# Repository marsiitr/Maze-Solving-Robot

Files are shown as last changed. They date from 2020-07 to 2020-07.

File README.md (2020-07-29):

# Maze-Solving-Robot
Srishti 2020

## Abstract

The Maze Solving Bot is a wireless bot. It is capable of solving any 2-D maze with the help of live video feed parsed by a python script. The speciality of this bot is that it can adapt itself to any maze and not one-kind in particular. Having a Four-wheel Omni drive, It aims to reach the ending point in the shortest time. If there are more than two ways out, then it works to solve the shortest path.

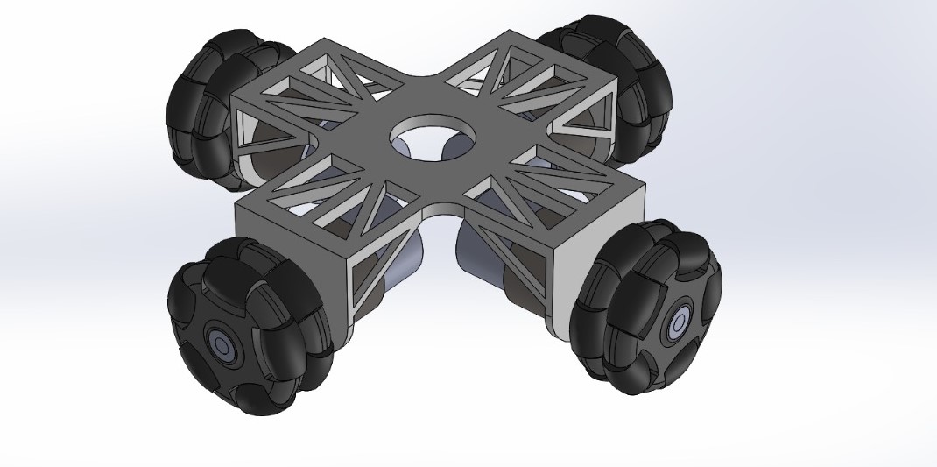
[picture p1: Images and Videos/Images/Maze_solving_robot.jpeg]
Final Product


## Motivation

<p align="justify">Maze solving bot is a simple and straightforward case where we can learn and experiment about path planning. The standard method of maze solving takes much time due to its trial and error methods. With the help of shortest path detection and robot live coordinates mapping, we look forward to improvising the olden methods.<br><br>A maze in the real-world can represent roads and traffic. All of us want to know the best way to go to work, school etc.  In the journey, we experience all sorts of obstructions like traffic, diversions, intersections and dead-ends. This project gives us an insight into how to solve this problem. It helps us find the best and the shortest path to avoid these barricades as much as possible.</p>

## Components

* 2x Motor Driver L2899
* 4x DC () rpm Motors
* Nodemcu Esp8266
* 1x 12V DC Power Adapter
* 3D printed Chassis
* 4x Omni Wheels

## Workflow

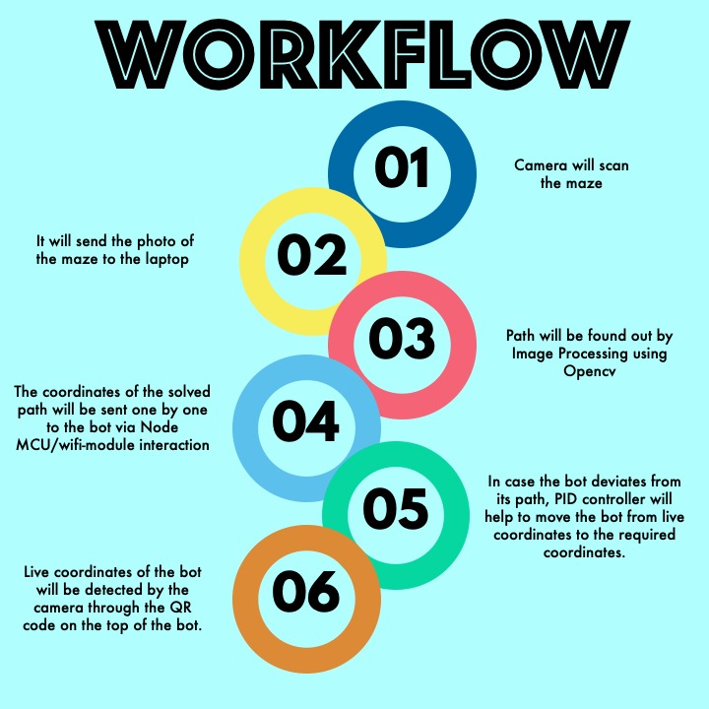
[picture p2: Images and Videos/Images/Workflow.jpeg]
Worflow Diagram


## Mechanical Aspect of the Design

### Chassis

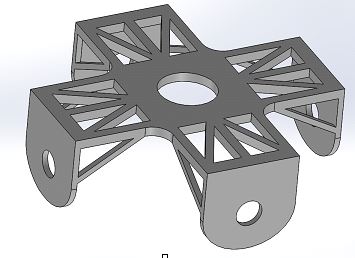
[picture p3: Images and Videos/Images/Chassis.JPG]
Chasis


<p align="justify">The main body of the robot is 3D printed using PLA(Polylactic Acid). It has the shape of a ‘plus’ sign. The dimensions of the chassis are about 14.5cm x 14.5cm x 5 cm. There are lightening holes present wherever possible to keep the weight of the chassis less</p>

### Drive type

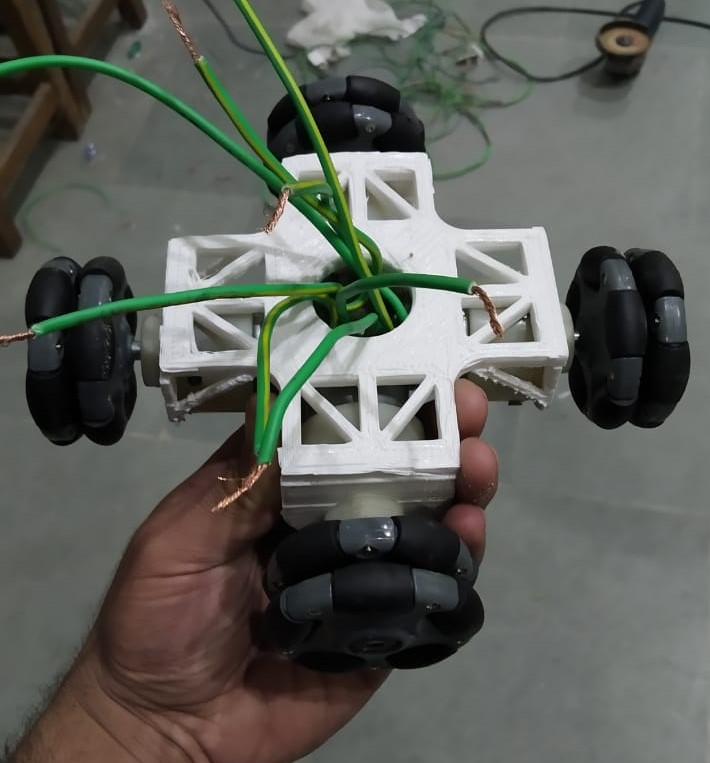
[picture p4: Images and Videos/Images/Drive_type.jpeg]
Drive _type


<p align="justify">The maze solving bot uses a 4 wheeled Omni type of drive. 2 sets of Omni wheels are perpendicular to the other set. The reason for this design is that the maze only consists of perpendicular junctions. Hence the working of the robot is highly simplified if we use 4 WD Omni.<br><br> 4 WD Omni in general has some limitations. It only takes 3 points to define a plane. Hence in most practical cases, the 4th wheel lies out of the plane. But in this project, we could dodge this limitation by 3D printing the chassis thus making it highly accurate.</p>

## Electronics Aspect of the Design

### Actuator

The robot uses four 12 volt- 100 rpm motors. These motors are relatively light, weighing a few hundred grams and overall have a small and compact size. Having a small body size is imperative for the robot to transverse through the narrow lanes of the maze..

### Microcontroller

* One of the biggest benefits of the NodeMCU is that it allows communication over a wifi-network, hence there is no need to keep it plugged into the device on which the source code is, the instructions can be easily sent over a wifi network.
* This allows the execution of the PID control equation to a significantly higher degree of precision.
* Completing both the tasks of receiving coordinates and controlling motors is done by Nodemcu. Coordinates are detected by scanning QR code.

### PID Control

* The PID control allows monitoring the progression of errors in the movements of the robot and making minute changes in the operation of the actuators to ensure a greater degree of precision in the robot’s movements.
* In our case, the robot had to move parallel to the co-ordinate axis only on a flat surface with minimal skidding of the wheels. This simplified our job many-fold, since now we focus only on the “proportional errors”, without considering the derivative of the integral terms.

## Cost Structure

| *Components* |*Cost(INR.)*|
|---|---|
| 2x Motor Driver L2899 | 250 |
| 2x DC () rpm Motors | 700 |
| Nodemcu Esp8266 | 350 |
| 12v Battery | 1000 |
| 3D printed Chassis | 800 |
| 4x Omni Wheels | 2200 |
| *Total* | *5300*  |

## Applications

* Reduce manual labour in waiting in hotels and in deliveries.
* Can be used in parking lots to direct the cars to the closest empty space.
* Future of driving is self-driving cars or fully automated cars 

## Limitations

* The Camera that we are using for image processing is attached to our laptop with wires, so that might become a bit hectic to handle.
* There has to be a minimum height above which Camera should be mounted, so for our maze solving bot show we need a spacious room, and we have to deal with a bunch of extra wires.

## Future Improvements

* Sensors can be added to the bot to avoid further immediate obstacles.

## Team Members

1. Akshat Gupta
2. [Sarthak Surolia](https://github.com/sarthak1420)
3. Sidhhart Gehlot
4. [Shanmathi Selvaraj](https://github.com/shan-mathi)
5. [Sneha Jain](https://github.com/snehajain02)
6. [Susmit Walve](https://github.com/susmitwalve)
7. [Suhani Jain](https://github.com/jainsuhani317)
8. [Yash Asati](https://github.com/yashasati53)

## Mentors

1. [Sanjeev Krishnan R.](https://github.com/SanjeevKrishnan)
2. Shubham Malviya

## References

<https://www.learnopencv.com/opencv-qr-code-scanner-c-and-python/>

<https://youtu.be/0u78hx-66Xk>

<https://github.com/marsiitr/DIC_Terrace_Farming>

<https://www.instructables.com/id/Controlling-Arduino-with-python-based-web-API-No-p/>

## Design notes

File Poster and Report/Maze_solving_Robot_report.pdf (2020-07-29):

# Maze solving Robot

## Srishti 2020 Project Report

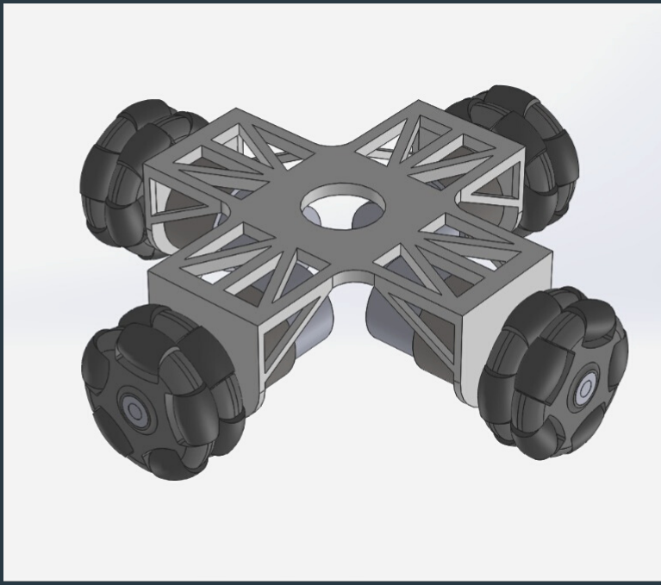
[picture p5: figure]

# INDEX

Team Members | 01
Abstract | 02
Motivation | 02
Workflow | 03
Mechanical aspects | 04
Electronic aspects | 05
Cost Structure | 08
Applications | 09
Limitations | 09
Further Improvements | 09
References | 10

# Team Members:

# Akshat Gupta Sarthak Surolia Shanmathi Selvaraj Siddharth Gehlot Sneha Jain Suhani Jain Susmit Walve Yash Asati

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
# Mentors:

Sanjeev Krishnan R.

# Shubham Malviya

1.
2.

1

# Abstract

The Maze Solving Bot is a wireless bot. It is capable of solving any 2-D maze with the help of live video feed parsed by a python script. The speciality of this bot is that it can adapt itself to any maze and not one-kind in particular. Having a Four-wheel Omni drive, It aims to reach the ending point in the shortest time. If there are more than two ways out, then it works to solve the shortest path.

# Motivation

Maze solving bot is a simple and straightforward case where we can learn and experiment about path planning. The standard method of maze solving takes much time due to its trial and error methods. With the help of shortest path detection and robot live coordinates mapping, we looked forward to improvise the olden methods.

A maze in the real-world can represent roads and traffic. All of us want to know the best way to go to work, school etc. In the journey, we experience all sorts of obstructions like traffic, diversions, intersections and dead-ends. This project gives us an insight into how to solve this problem. It helps us find the best and the shortest path to avoid these barricades as much as possible

2

# Workflow:

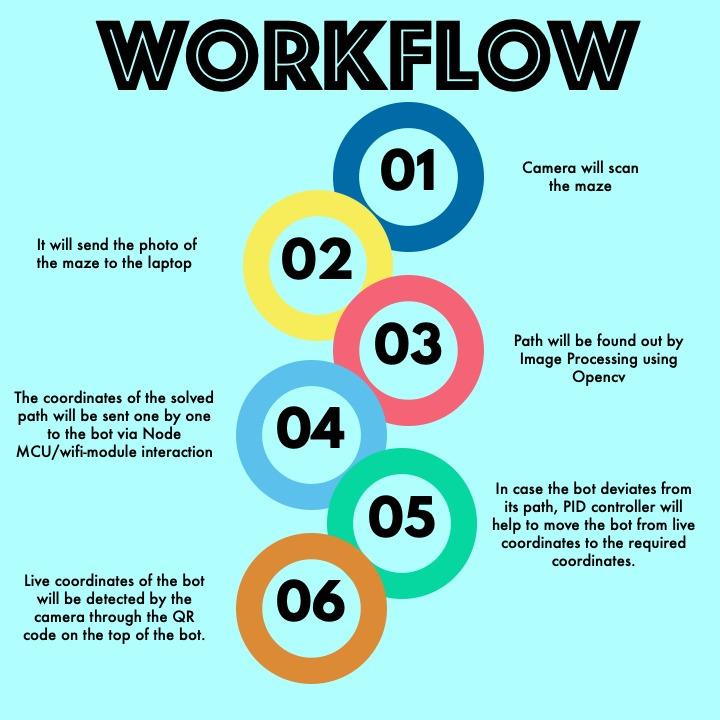
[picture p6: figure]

3

# Mechanical Aspects:

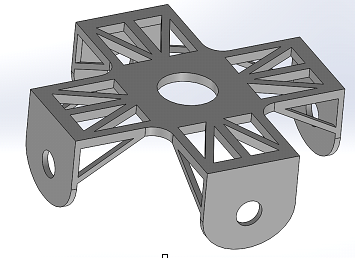
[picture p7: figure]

## 1.Chassis:

The main body of the robot is 3D printed using PLA(Polylactic Acid). It has the shape of a ‘plus’ sign. The dimensions of the chassis are about 14.5cm x 14.5cm x 5 cm. There are lightening holes present wherever possible to keep the weight of the chassis low.

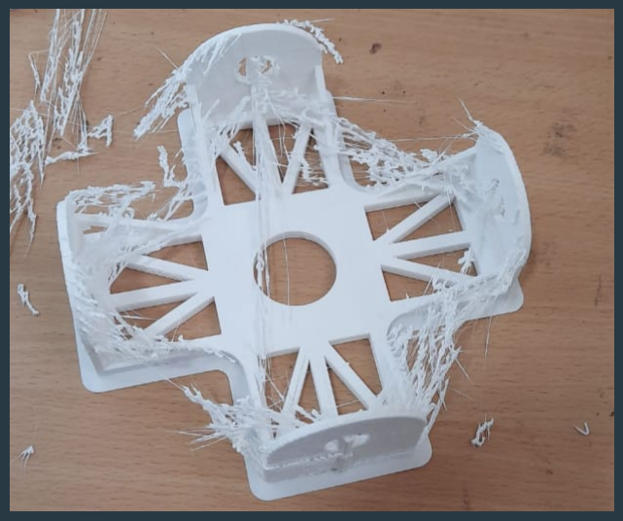
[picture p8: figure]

## 2. Drive type

The maze solving bot uses a 4 wheeled Omni type of drive. 2 sets of Omni wheels are perpendicular to the other set. The reason for this design is that the maze only consists of perpendicular junctions. Hence the working of the robot is highly simplified if we use 4 WD Omni. 4 WD Omni in general has some limitations. It only takes 3 points to define a plane. Hence in most practical cases, the 4th wheel lies out of the plane. But in this project, we could dodge this limitation by 3D printing the chassis thus making it highly accurate.

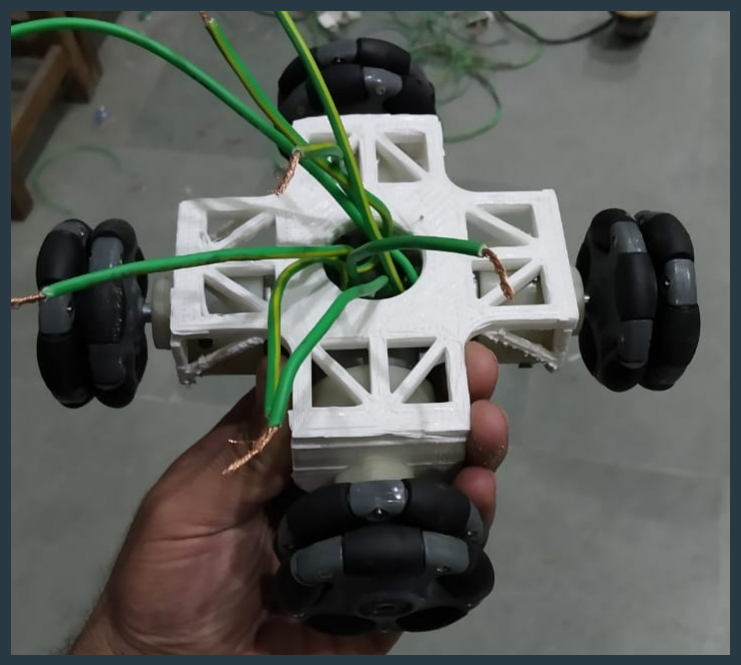
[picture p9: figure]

4

# Electronic Aspects:

## 1.Actuator:

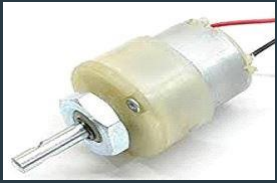
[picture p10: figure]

The robot uses four 12 volt- 100 rpm motors. These motors are relatively light, weighing a few hundred grams and overall have a small and compact size. Having a small body size is imperative for the robot to transverse through the narrow lanes of the maze.

There were some issues regarding the four motors not delivering equal amount of torque, resulting in the robot changing its orientation. This is where the PID control was employed to ensure the robot transverses the maze immaculately. Since the robot is designed to move on flat surfaces, none of the four wheels would lose contact with the surface, ensuring that the robot would not rotate about one of its wheels.

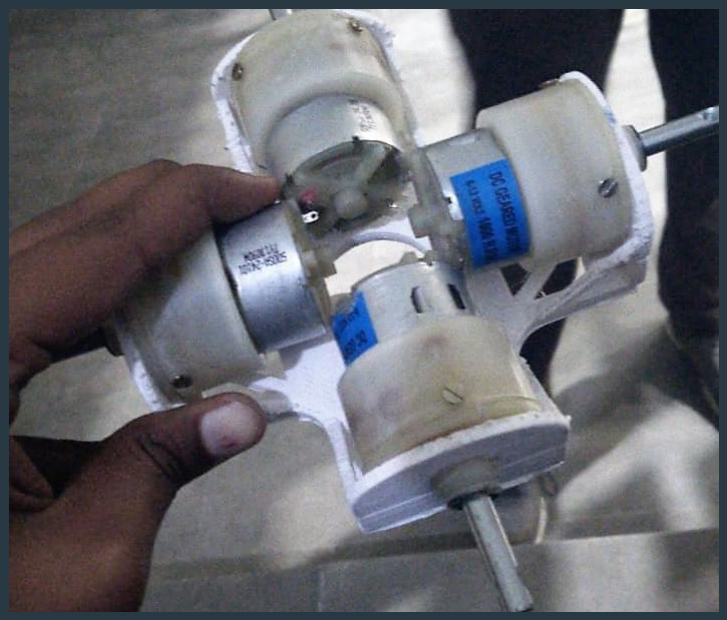
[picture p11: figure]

5

## 2. Microcontroller

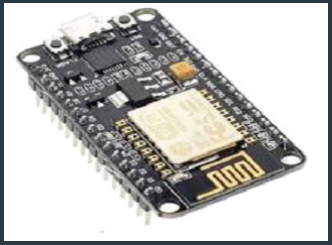
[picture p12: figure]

A Node Microcontroller Unit a.k.a Node MCU was used as a microcontroller. It facilitates an open-source software for hardware development. It is small, lightweight, extremely efficient and is built on a “System on Chip” called ESP8266, which is relatively less costly.
One of the biggest
benefits of the NodeMCU is that it allows communication over a wifi-network, hence there is no need to keep it pluged into the device on which the source code is, the instructions can be easily sent over a wifi-network, if neccesary, parsed with the help of a python script. The clock speed of the NodeMCU is close to 80 MHz, ensuring significant speed and preventing too much delay between the parsing of instructions and operation of the actuators. Also,this allows the execution of PID control equation to a significantly higher degree of precision.completing both the tasks of recieving coordinates and controlling motors is done by nodemcu. Coordinates are detected by scanning the QR code

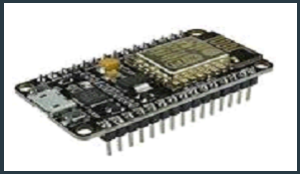
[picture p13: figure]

6

## 3. PID Control

The PID control allows monitoring the progression of errors in the movements of the robot and making minute changes in the operation of the actuators to ensure a greater degree of precision in the robot’s movements.

In our case the robot had to move parallel to the co-ordinate axis only on a flat surface with minimal skidding of the wheels. This simplified our job many-fold, since now we focus only on the “proportional errors”, without considering the derivative or the integral terms. Also, the orientation of the robot had to be taken into account, since it was always possible that one of the parallel sets of wheels moves faster than its counterpart, hence resulting in a rotation of the robot’s chassis to rotate and become disoriented.

We made use of a python script to determine the robot’s current coordinates as well as its orientation with respect to the co-ordinate axis. This allowed us to operate the actuators to bring the robot to its correct orientation and position.To change the orientation, all four wheels rotate in clockwise or counter-clockwise manner , until the robot gets as close to the desired orientation as possible.

For handling errors in the position, we handle movement along the x and y-axis separately (the robot always moves along a path parallel to the co-ordinate axis).The speed of the robot can be altered in accordance with the equation v=kp*(x-x’) where- x-current position of the robotx’-desired position of the robotkp- error constant, determined through trials.

As one can note, the robot’s speed gets reduced as we get closer to the desired position, the rate of decrease depending significantly on the constant kp. Similar arguments can be applied to the movements along the y-axis. The constant kp depends on the material of the wheels, the traction available off the surface, the amount of skidding and some inevitable manufacturing defects. The value remains somewhere between 0.03- 0.5 but can vary greatly, thus requiring a number of trials to determine.

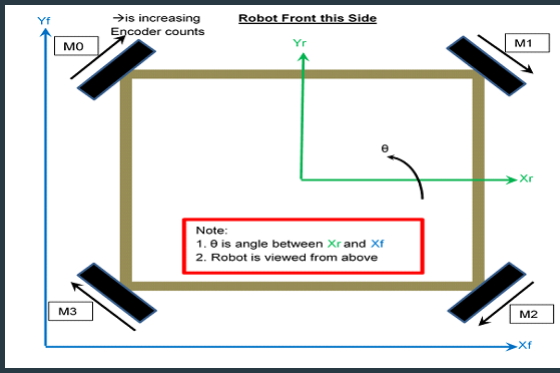
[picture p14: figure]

7

# Cost Structure:

COMPONENTS

2X MOTOR DRIVER L2899

4X DC () RPM MOTORS

NODEMCU ESP8266

8

COST(INR)

12V BATTERY

3D PRINTED CHASSIS

4X OMNI WHEELS

250

700

350

1000

800

2200

TOTAL | 5300

# Applications:

Our maze solving bot is a four-wheel chassis. It is planer even in uneven terrains. It can be used as a food and other things delivery system for high altitude army posts. Usually, a drone will not get a signal in such high altitudes. Moreover, this bot uses image processing before starting to solve the maze, which comes in handy for areas having low signals catching capacities.

# Limitations:

The Camera that we are using for image processing is attached to our laptop with wires, so that might become a bit hectic to handle.

There has to be a minimum height above which Camera should be mounted, so for our maze solving bot show we need a spacious room, and we have to deal with a bunch of extra wires.

9

Future of driving is self-driving cars or fully automated cars. While parking in a parking area. They are a sophisticated version of our maze solving bot. Wherein obstacles are other cars and pillars. There can be a series of cameras on the wall which takes a whole 2D image of the parking area and uses image processing to solve the maze (or parking area) and tell the best possible coordinate to know where to park the car. So these can be seen as daily applications of our bot.

# Further Improvements

Sensors can be added to the bot to avoid further immediate obstacles.

# Reference Links:

10

1.QR code Scanner
https://www.learnopencv.com/opencv-qr-code-scanner-c-and-python/
2. Bot Traversal
https://youtu.be/0u78hx-66Xk
3. DIC-Terrace_farming_documentation https://github.com/marsiitr/DIC_Terrace_Farming
4. controlling Arduino with Python based API https://www.instructables.com/id/Controlling-Arduino-with-python-based-web-API-No-p/
5. Solidworks
https://www.solidworks.com/

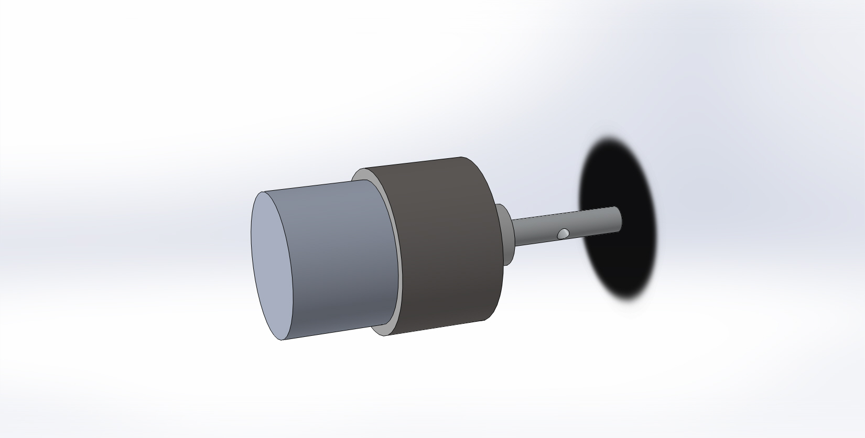
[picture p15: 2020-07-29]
Mechanical Design/1000RPM_DC_VegaMotor.JPG

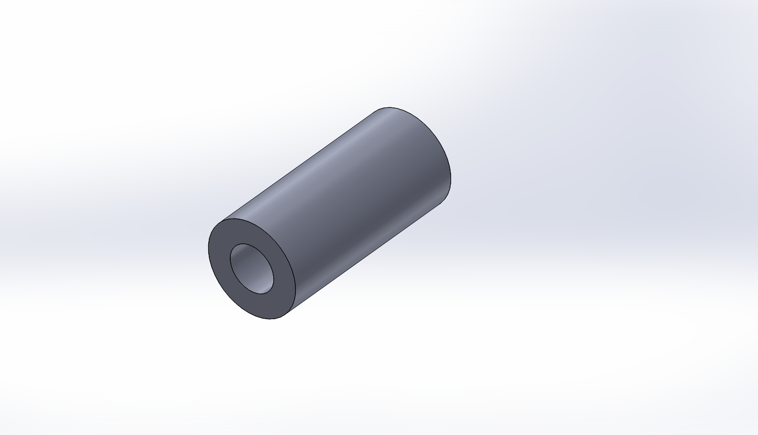
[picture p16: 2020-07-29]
Mechanical Design/Shaft_Coupling.png

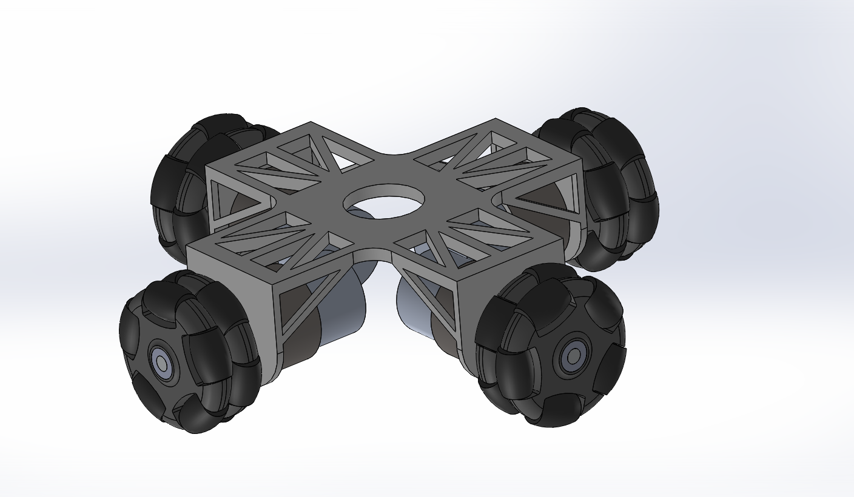
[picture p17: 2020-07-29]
Mechanical Design/Maze_Solving_Bot.png

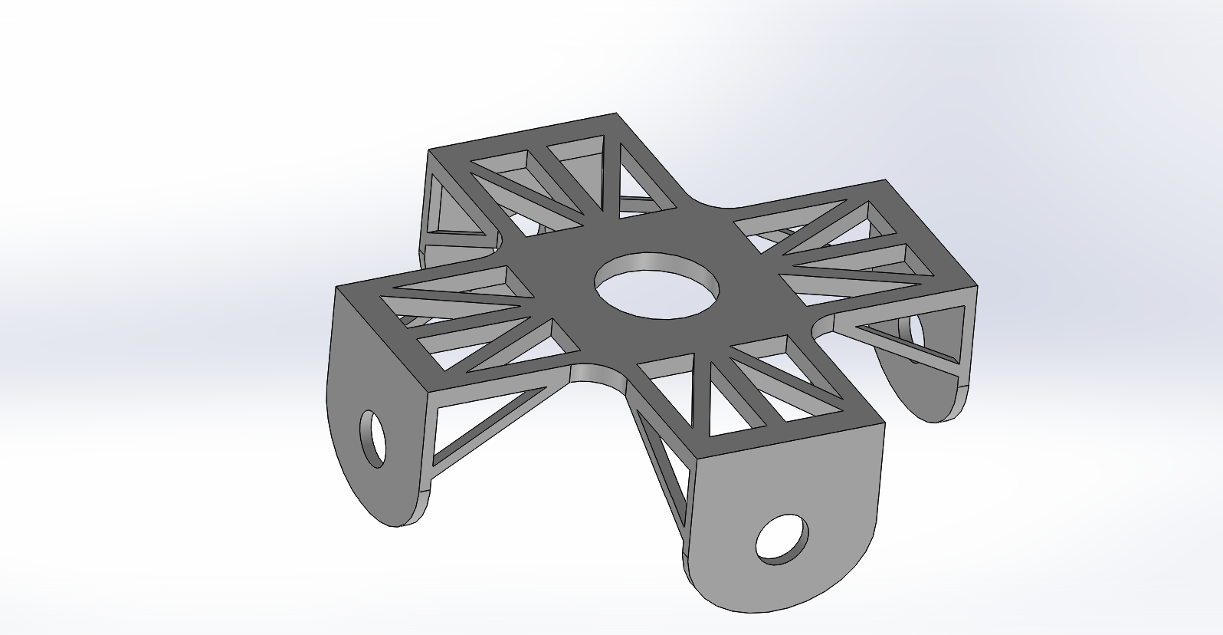
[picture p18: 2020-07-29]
Mechanical Design/Maze_Solving_Bot_Chassis.png

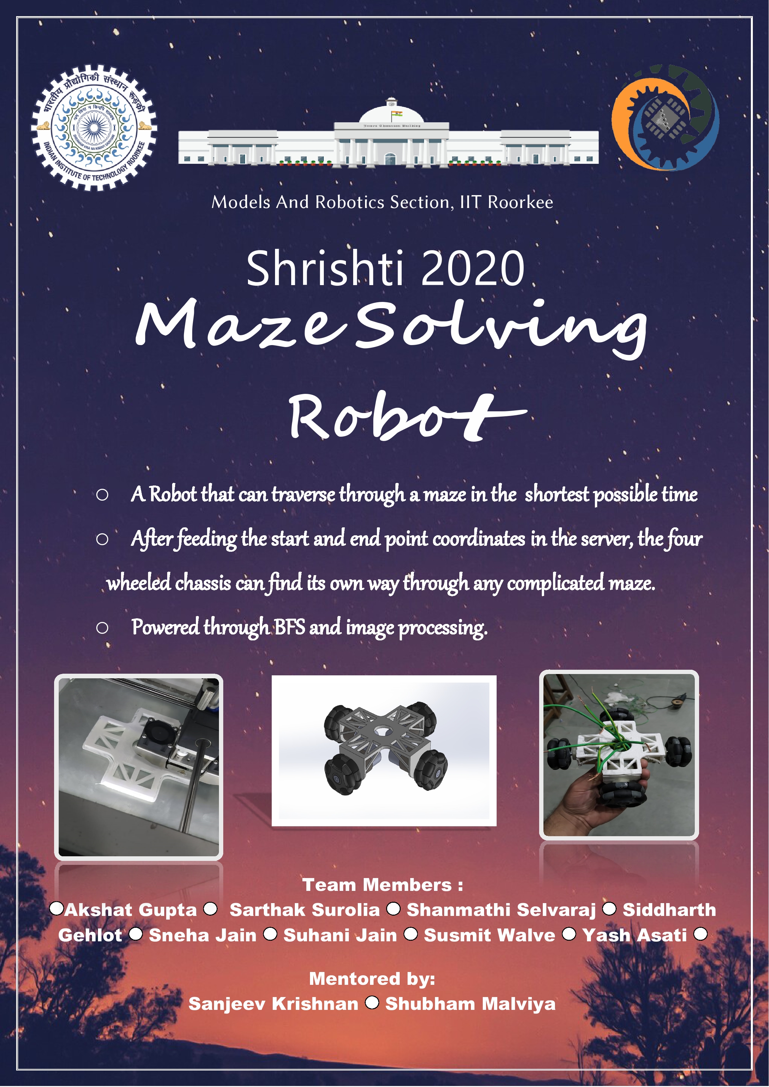
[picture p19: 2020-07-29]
Poster and Report/Poster.jpg

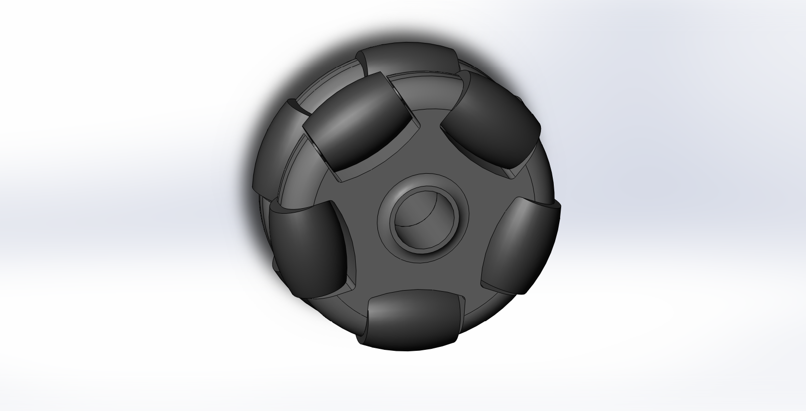
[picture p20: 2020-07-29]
Mechanical Design/Omni_Wheel_58mm.png

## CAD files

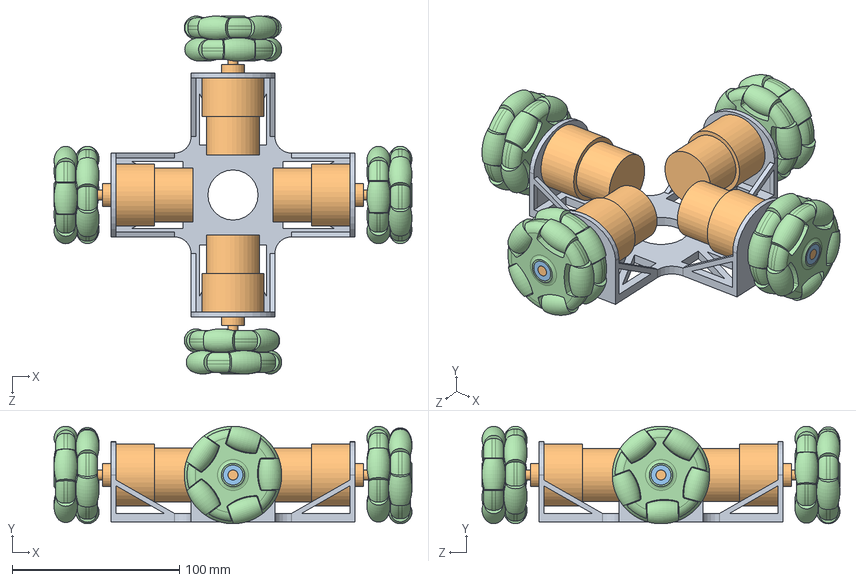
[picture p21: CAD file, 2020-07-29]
Mechanical Design/Maze_Solving_Bot.SLDASM
214.0 x 58.3 x 214.0 mm
Maze_Solving_Bot_Chassis
1000RPM_DC_VegaMotor x 4
Shaft_Coupling x 4
Omni_Wheel_58mm x 4

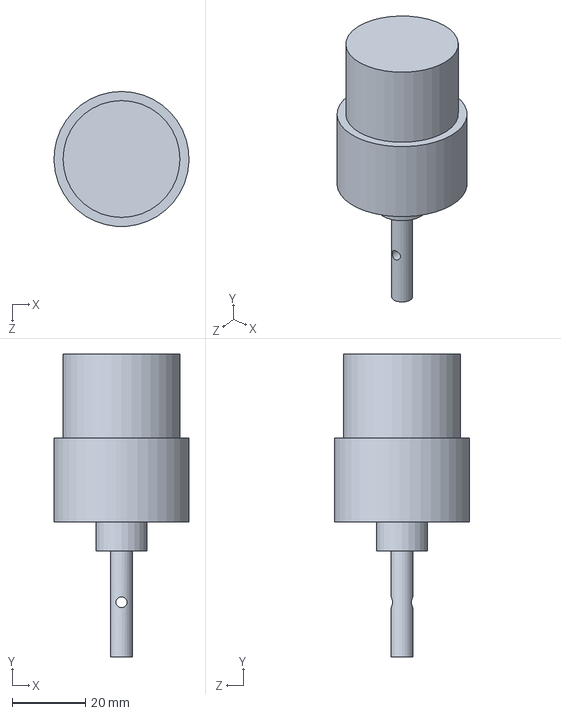
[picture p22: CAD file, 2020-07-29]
Mechanical Design/1000RPM_DC_VegaMotor.SLDPRT
37.0 x 83.0 x 37.0 mm

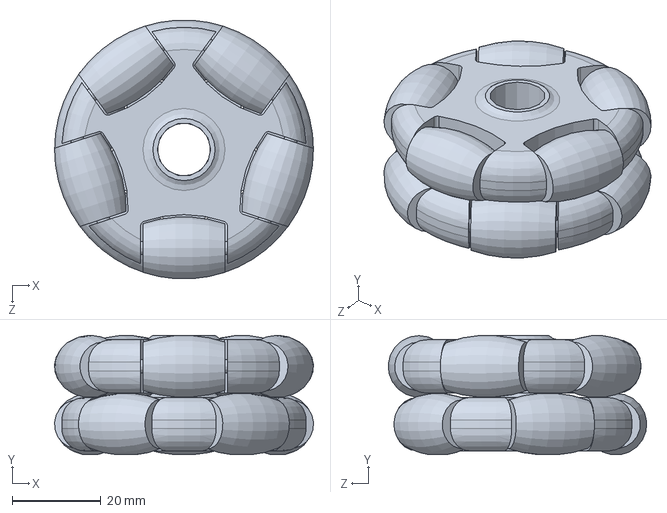
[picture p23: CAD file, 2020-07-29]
Mechanical Design/Omni_Wheel_58mm.SLDPRT
58.3 x 26.9 x 58.1 mm

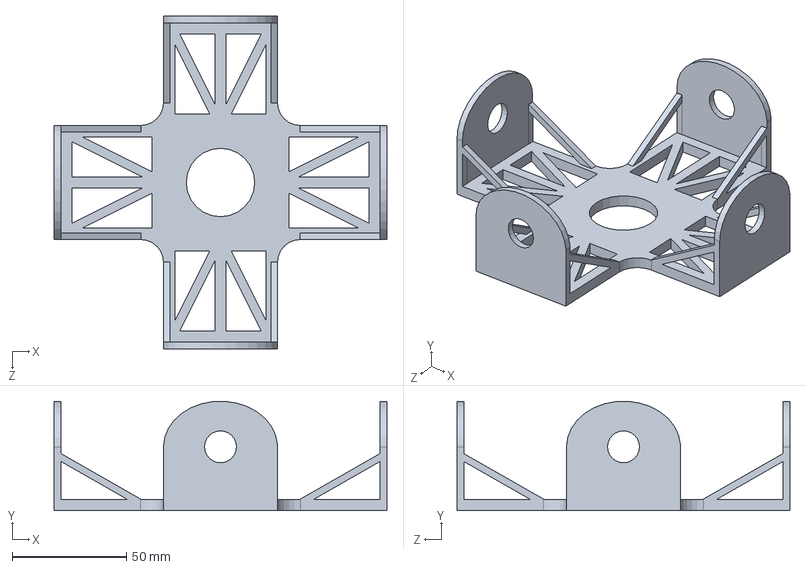
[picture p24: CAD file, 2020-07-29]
Mechanical Design/Maze_Solving_Bot_Chassis.SLDPRT
146.0 x 47.9 x 146.0 mm

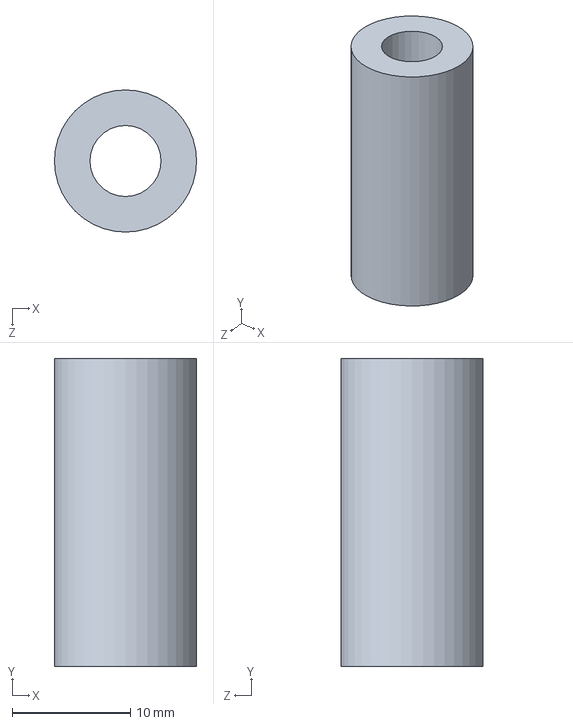
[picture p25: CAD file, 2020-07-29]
Mechanical Design/Shaft_Coupling.SLDPRT
12.0 x 26.0 x 12.0 mm

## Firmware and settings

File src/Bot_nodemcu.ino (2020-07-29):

//PID CONTROL
//********************
double r,aprev=0,v,kp=0.5,kd=0.45;
// r->radius of robot body's circumcircle
//apprev->error in orientation in previous iteration,initially set to zero
// kp,kd->PID constants
//v->robot speed
void angle(double a)//rectifying the error in orientation
{
  double t=(a*r)/v;
  double output= (kp*a+kd(a-aprev)/t);
  t=(output*r)/v;
  digitalWrite(in1a,HIGH);
  digitalWrite(in2a,LOW);
  digitalWrite(in1b,HIGH);
  digitalWrite(in2b,LOW);
  digitalWrite(in1c,HIGH);
  digitalWrite(in2c,LOW);
  digitalWrite(in1d,HIGH);
  digitalWrite(in2d,LOW);
  analogWrite(enableA,v);
  analogWrite(enableB,v);
  analogWrite(enableC,v);
  analogWrite(enableD,v);
  aprev=a; 
  delay((int)t);
}
void getPosition(double &x,double &y,double &xf,double &yf)
                                     //extracts robot co-ordinates via live video feed
{
  x=//robot's current x-co-ordinate
  y=//robot's current y-co-ordinate
  xf=//robot's desired x-co-ordinate
  yf=//robot's desired y-co-ordinate
}
long long splitmix64(long long  x)
{
 x+=0x9e3779b97f4a7c15; 
 x=(x^(x>>30))*0xbf58476d1ce4e5b9; 
 x=(x^(x>>27))*0x94d049bb133111eb; 
 return x^(x>>31);
}
void set_speed(double v)
{
  analogWrite(enableA,v);
  analogWrite(enableB,v);
  analogWrite(enableC,v);
  analogWrite(enableD,v);
}
void error(double c,double cf,int f)//f=1 for movement along y-axis f=0 for movement along x-axis
{
 double err=(cf-c); 
 double change_vel=err;
 v-=change_vel;//as the robot gets closer to the target,the velocity of the robot decreases
 long long FIXED_RANDOM=chrono::steady_clock::now().time_since_epoch().count();
 FIXED_RANDOM=splitmax64(FIXED_RANDOM+kp);
 set_speed(v*FIXED_RANDOM);   
}
void setup()
{
 pinMode(in1a,OUT); pinMode(in2a,OUT); 
 pinMode(in1b,OUT); pinMode(in2b,OUT);
 pinMode(in1c,OUT); pinMode(in2c,OUT);
 pinMode(in1d,OUT); pinMode(in2d,OUT);
 pinMode(enableA,OUT); pinMode(enableB,OUT); pinMode(enableC,OUT); pinMode(enableD,OUT); 
 v=//setting initial robot speed ,over the course of the maze, speed does not exceed this value
}
void loop() 
{
 double x,y,xf,yf; // x,y->initial position of robot xf,yf->position of robot as to where it should be
 double a=(yf-y)/(xf-x);  
 angle(a);
 if(xf!=x)
 {
 error(x,xf,0); 
 }   
 else
 {
 error(y,yf,1); 
 }
 delay(2000); 
}


//**************
//receiving coordinates from laptop by NodeMCU
//**************
void loop()
{
const char* ssid     = "asati";
const char* password = "naibatana";

WiFiServer server(80);
unsigned long currentTime = millis();
unsigned long previousTime = 0; 
const long timeoutTime = 2000;

void setup() {
  Serial.begin(115200);
  Serial.print("Connecting to ");
  Serial.println(ssid);
  WiFi.begin(ssid, password);
  while (WiFi.status() != WL_CONNECTED) {
    delay(500);
    Serial.print(".");
  }
  Serial.println("");
  Serial.println("WiFi connected.");
  Serial.println("IP address: ");
  Serial.println(WiFi.localIP());
  server.begin();
}

void loop(){
  WiFiClient client = server.available();   // Listen for incoming clients

  if (client) {                             // If a new client connects,
    Serial.println("New Client.");          // print a message out in the serial port
    String currentLine = "";                // make a String to hold incoming data from the client
    currentTime = millis();
    previousTime = currentTime;
    String tmp ="";
    while (client.connected() && currentTime - previousTime <= timeoutTime) { // loop while the client's connected
      currentTime = millis();         
      if (client.available()) { // if there's bytes to read from the client,
        char c = client.read();
        tmp+=c;
//        
                    // read a byte, then
        Serial.write(c);                    // print it out the serial monitor
        if (c == '\n') {                    // if the byte is a newline character
          // if the current line is blank, you got two newline characters in a row.
          // that's the end of the client HTTP request, so send a response:
          if (currentLine.length() == 0) {
            // HTTP headers always start with a response code (e.g. HTTP/1.1 200 OK)
            // and a content-type so the client knows what's coming, then a blank line:
            client.println("HTTP/1.1 200 OK");
            client.println("Content-type:text/html");
            client.println("Connection: close");
            client.println();
            client.println();
            // Break out of the while loop
            break;
          } else { // if you got a newline, then clear currentLine
            currentLine = "";
          }
        } else if (c != '\r') {  // if you got anything else but a carriage return character,
          currentLine += c;      // add it to the end of the currentLine
        }
      }
    }    
          
    client.stop();
    Serial.println("Client disconnected.");
    Serial.println(tmp);
    Serial.println("");
  
  int jk=5;
  long rj = 0;
  while(isDigit(tmp[jk])){
   rj = (rj*10)+(((int)tmp[jk])-48); 
   jk++;
  }
  Serial.println(rj);}
  //this(rj) is the target x_coordinate received by nodemcu;
  //similarly current x_position,current y_position,target y_coordinate will be received by nodemcu and fed to PID.
}
